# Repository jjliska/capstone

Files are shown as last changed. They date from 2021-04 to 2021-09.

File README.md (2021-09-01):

# AME 486 - Capstone - Reflection  

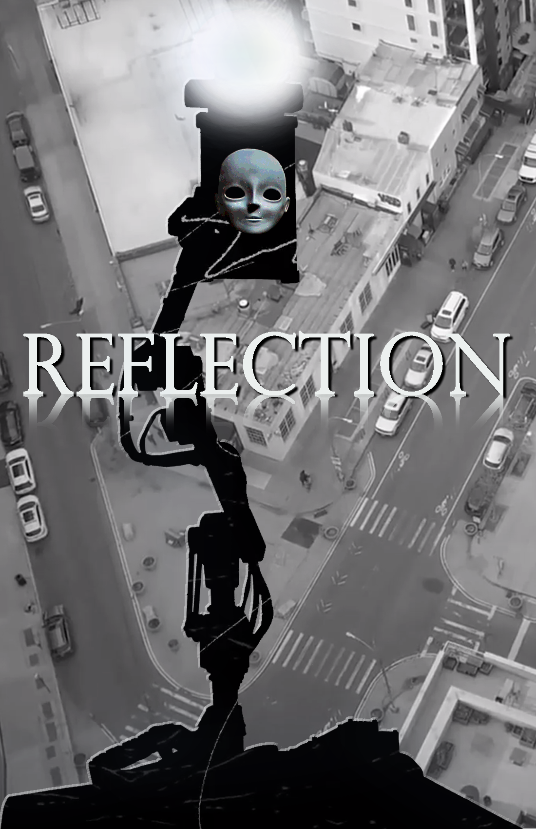
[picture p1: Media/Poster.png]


#### Table of Contents  
&ensp;[Group Members](#Group-Members)  
&ensp;[Project Description](#Project-Description)  
&ensp;[Capstone Video](#Capstone-Video)  
&ensp;[Improvements and Issues](#Improvements-and-Issues)  
&ensp;[Demo Videos](#Demo-Videos)  
&ensp;[Explanations](#Explanations)  
&ensp;[Links](#Links)  
&ensp;[References](#References)  

## Project Description  
&ensp;"Reflection" is an immersive, interactive art instillation that attempts to give people a form of interaction during isolation. The installation consists of two key components, the user and the robot cordially named Dum-E. Users interact with the piece by walking around in the scene, and looking at the robot. The machine learning algorithms will attempt to follow the person in the scene and react to their location and emotion. When Dum-E identifies a new emotion it will react with its own emotion and play a song at a specific location given where the user is.

## Group Members  
&ensp;<sup>[Back to Top](#AME-486---Capstone---Reflection)</sup>  
&ensp;[Albert Bang](https://albertbang3000.wixsit.com/) - Unity/Animator  
&ensp;[Ivan Mendoza](https://ivanmendozaportfolio.com/) - Programming/Building  
&ensp;[Jack Carroll](https://soundcloud.com/sodonttalksmack) - Sound Designer  
&ensp;[Joshua Liska](https://www.linkedin.com/in/joshua-liska-34a4b77b/) - Programming/Design/Engineering/Documentation

## Capstone Video  
&ensp;<sup>[Back to Top](#AME-486---Capstone---Reflection)</sup>  
IMAGE ALT TEXT HERE (https://www.youtube.com/watch?v=mnH26vL3UBw)

## Improvements and Issues  
&ensp;<sup>[Back to Top](#AME-486---Capstone---Reflection)</sup>  
#### Quick Links for Issues
&ensp;[Emotion and Facial Tracking](#Emotion-and-Facial-Tracking)  
&ensp;[Serial Read Issue](#Serial-Read-Issue)  
&ensp;[Speed Under Load](#Speed-Under-Load)  
&ensp;[Thermal Deformation](#Thermal-Deformation)  
#### Emotion and Facial Tracking  
##### The Problem  
&ensp;The consistency of the facial tracking system we used was not the most precise due to several reasons. One such reason, we suspect, is the camera quality was reduced so that it would run faster, as well as the dataset we used was most likely not precise enough for the system.  
&ensp; Another issue we faced was the lag caused by the emotion rendering system. We ended up setting this to run four to six times a minute for multiple reasons. One being the speed of the program was greatly increased when the emotions were only extracted several times a minute as well as the facial expressions of the unity program were allowed time to gently fade into each other. The emotion tracking was also not the most consistent, the dataset we used returned a roughly 66% accurate reading. It also has particular issues tracking emotion if there isn't enough light, hence the addition of a light on top of the arm.
##### Potential Solutions   
&ensp;A solution is to use a far more powerful computer to render the program in. This would allow for greater frame rates as well as being able to render emotions more accurately. A good small form factor computer for this would be an nvidia jetson, although it is an arm architecture processor, which would force us to either recompile the unreal engine source into an aarch64 architecture. We attempted to do this as well as exporting a unity project as an apk to run on android 11, however it didn't work as there were driver conflicts. 
&ensp;The facial expression detection dataset should be trimmed and retrained to allow for better facial expression tracking specifically in low light conditions and retrain it with our faces as a training set. We could also use some sort of recursive learning that retrains the model once a given number of facial frames are taken from the camera. This would require quite a substantial amount of processing power though to allow everything else to run efficiently.
#### Serial Read Issue
##### The Problem  
&ensp;There seems to be an issue with the Serial.Read on the microcontroller, for some reason even when reading bytes and converting to a data structure it will occasionally throw an error. This will end up crashing the program, and was initially the reason we needed so many try-catch and an eeprom safety net for if the program were to crash we could smoothly go back to the starting position and restart the program.
##### Potential Solutions  
&ensp;From many of the statements online this seems to be an issue with the arduino String data structure and it occasionally corrupts the memory. That being said we have a one way serial communication and the python program, running on a seperate computer, is crashing first. As of yet we do not have a concrete solution, simply possible conjecture that may help lead to a solution.
#### Speed Under Load  
##### The Problem  
&ensp;The speed is greatly affected under the complete load of the arm, roughly 1.3kgs. This causes us to either offset the amount of smoothness in the arm to consistently track the face, or to reduce the speed. We chose to reduce both slightly so they remain hand in hand. We attempted to limit this effect by creating a smoothing algorithm that attempted to take this into account.  
&ensp;[Smoothing Algorithm](#Smoothing-Algorithm)  
##### Potential Solutions   
&ensp;The solution is to, again, increase the torque of the motors so that they are constantly running efficiently and are not being damped by the load on the system. This would allow them to greatly increase their speed and accuracy while still maintaining a level of smoothness. To accomplish the amount of speed and accuracy for a real world application this item would need roughly a1 = 80kgs/cm, a2 = 60kgs/cm, a3 = 40kgs/cm, and a4 = 40kgs/cm. However these would most likely not be servo motors as stepper motors would allow us much more versatility than the servos, as well as a much sturdier mounting system through their metal chassis.
#### Thermal Deformation  
##### The Problem  
&ensp;Since everything was printed in PLA there wasn't much resistance to the motor reaching peak torque and amperage pull began giving off a lot of heat. This then caused the PLA to deform under tension, as it is being pulled between the gear and the tensioning bracket. This caused warping in the form of the motor mount which eventually led to a loss of torque as the motor would pull forward and loosen tension on the belt, forcing the arm to skip steps.
##### Potential Solutions  
&ensp;The solution would be to either print the part in a different material, such as ABS which has higher thermal resistance or, as a more long term solution, replacing a2 (the middle arm motor) with a higher torque motor so it is more efficient under load.

## Demo Videos
&ensp;<sup>[Back to Top](#AME-486---Capstone---Reflection)</sup>  
### Unity Demo
IMAGE ALT TEXT HERE (https://www.youtube.com/watch?v=sWtO3qcnU5k)
### Tracking Demo
IMAGE ALT TEXT HERE (https://www.youtube.com/watch?v=6vG7myi-orQ)
### Smoothing Demo
IMAGE ALT TEXT HERE (https://www.youtube.com/watch?v=c3GQ3jPTU7w)
### Alpha Demo
IMAGE ALT TEXT HERE (https://www.youtube.com/watch?v=l52GL87oeng)

## Explanations
&ensp;<sup>[Back to Top](#AME-486---Capstone---Reflection)</sup>

#### Quick Links for Explanations
&ensp;[End Effector](#End-Effector)  
&ensp;[Machine Learning Data](#Machine-Learning-Data)  
&ensp;[ML Facial Data to Movement](#ML-Facial-Data-to-Movement)  
&ensp;[Smoothing Algorithm](#Smoothing-Algorithm)  
&ensp;[Hardware](#Hardware)  
&ensp;[Other Explanations](#Other)  

### End Effector
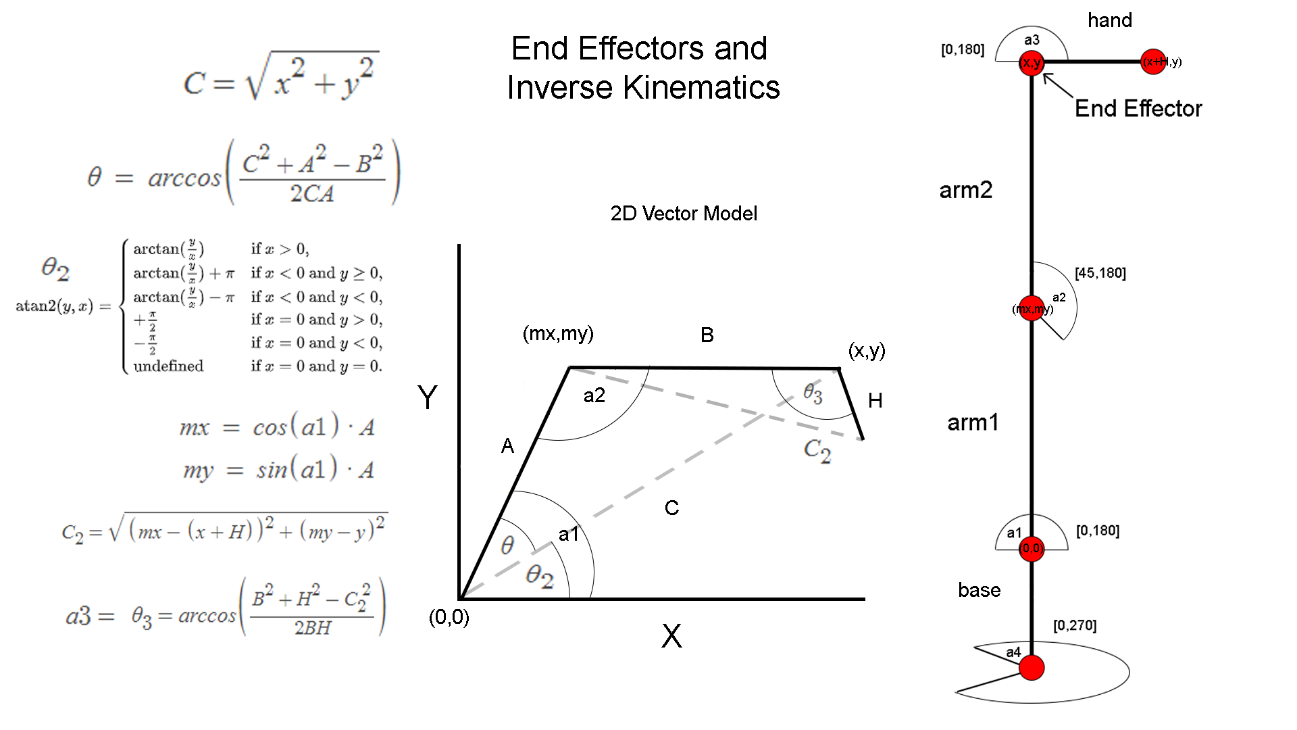
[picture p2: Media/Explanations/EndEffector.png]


&ensp;Inverse kinematics works via the premise that you know the base is 0,0 and the end effector is at some given point (x,y). Every shape can be then broken into triangles which have a given total angle. You can then determine this angle using the law of tangents and law of cosines. These allow you to determine the angle given arm lengths and positional data. For example, our arm has four degrees of freedom, three in the X and Y plane and one in the Z plane. We use two of the degrees of freedom to extend and retract the arm and a third to stabilize the "hand" and LCD attached to it. The fourth degree of freedom is used for Z rotation which is a simple trigonometry sin and cos function to calculate where the point is in a 3d space.

<details><summary>Python Script</summary>
<p>
  
```python
def lawOfCosines(a,b,c):
  return np.arccos((a**2+b**2-c**2) / (2.0*a*b))

def distance(x1,y1,x2,y2):
  return np.sqrt((x1-x2)**2+((y1-y2)**2))

def distanceMidArm(angle):
  opp = np.cos(angle) * arm1
  adj = np.sin(angle) * arm1
  return opp, adj

...

def angles(x,y):
  dist = distance(x,y,0,0)
  D1 = np.arctan2(y,x)
  D2 = lawOfCosines(dist,arm1,arm2)
  A1 = D1 + D2
  A2 = lawOfCosines(arm1,arm2,dist)
  return A1, A2
  
def rotateX(ox,x,angle):
  return ox+np.cos(angle)*(x-ox)

def rotateZ(ox,x,angle):
  return np.sin(angle)*(x-ox)
  
...
  
a1, a2 = angles(x,y)
mx, my = distanceMidArm(a1)
dist = distance(mx,my,x+hand,y)
#a3 is between arm2 and hand
if my <= y:
  a3 = lawOfCosines(arm2,hand,dist)
else:
  a3 = np.radians(360)-lawOfCosines(arm2,hand,dist)

#a4 is z rotation
a4 = np.radians(zRotation)
```

&ensp;[From capstoneV12_FINAlRELEASE.py](https://github.com/jjliska/capstone/blob/main/Code/Python/capstoneV12_FINALRELEASE.py)

</p>
</details>

### Machine Learning Data  
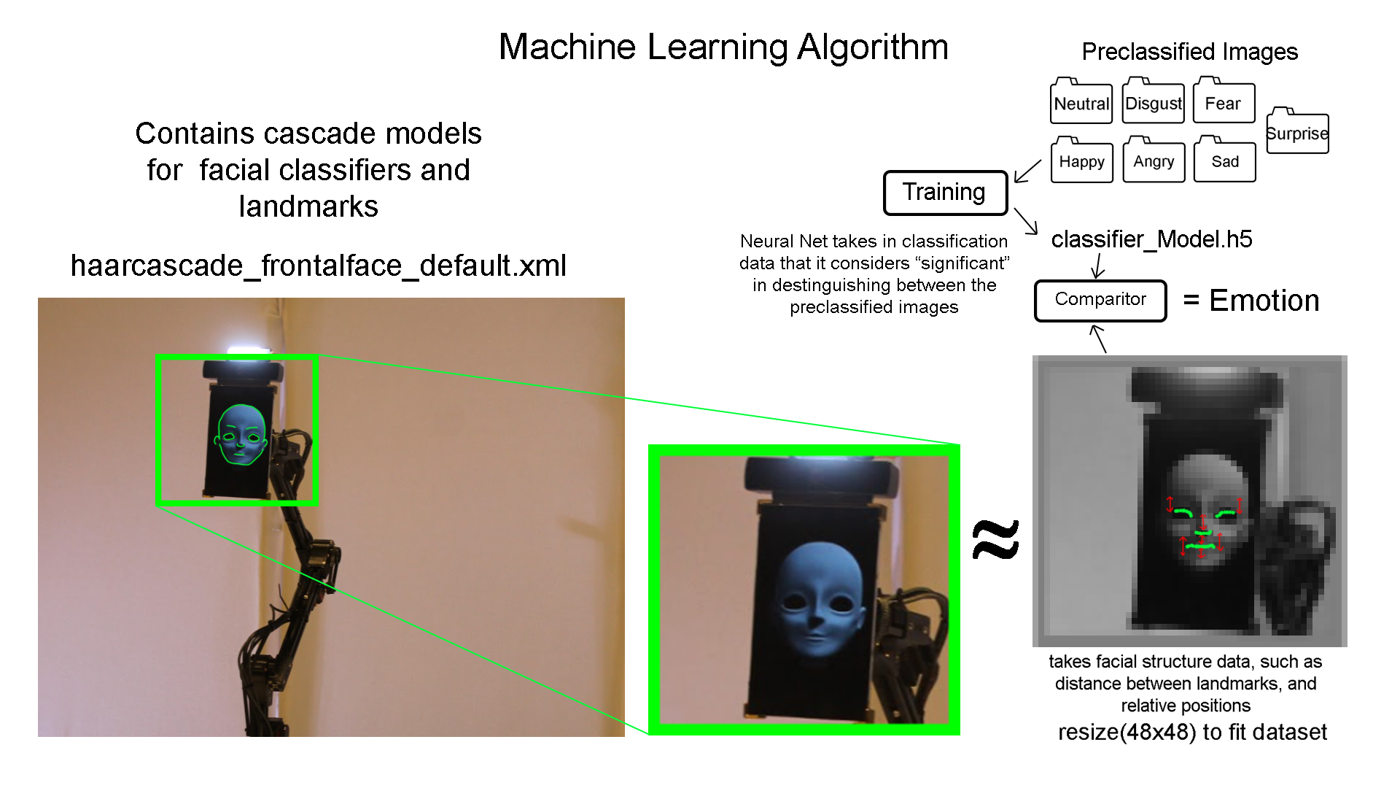
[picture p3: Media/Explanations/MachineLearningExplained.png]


&ensp;We use a pre classified dataset available in the openCV library, this is a visual library for machine learning. The pre classified haarcascade_frontalface_default.xml has pre classifications for significant landmarks of the face, for instance the edge of the face is a fairly distinct shape that can be recognized as separate from most objects in everyday life. This allows us to find exactly in frame where the face is. It returns a face(x,y,w,h) object that gives us facial bounding data. We then use that box created by the openCV haarcascade to crop out what we consider the "face" and convert it into a 48x48 pixel image. This is then passed to a classifying model that finds facial data points and compares it to another pre classified model that contains definitions for "emotion" which is a fairly hard for computer vision to assume. This is due to many people having different facial structures and what they consider the emotion on their face. Although this is fairly hard the trained model we used had a 66% accuracy. Althought it often tended to find that I was angry, as my neutral face looked angry to it.

<details><summary>Python Script</summary>
<p>

```python
cascPath = "haarcascade_frontalface_default.xml"
faceCascade = cv2.CascadeClassifier(cascPath)
modelPath = "model_35_91_61.h5"
emotion =  ['Anger', 'Disgust', 'Fear', 'Happy', 'Sad', 'Surprise', 'Neutral']
model = keras.models.load_model(modelPath)

...

    gray = cv2.cvtColor(frame, cv2.COLOR_BGR2GRAY)

    # Sets the face to gray, scales it, and then sets min neighbor and min size
    # These all help in removing false positives that the program sees and to reduce error.
    faces = faceCascade.detectMultiScale(
      gray,
      scaleFactor=1.2,
      minNeighbors=10,
      minSize=(30, 30)
    )

...

    # Draw a rectangle around the faces
    for (x, y, w, h) in faces:
      # Every second get the emotion written on the face via a 48*48
      # "facial structure" which pulls bounding data and refers to a trained model
      if getMood:
        # Gets the face, sets it to a 48*48 size frame and then parses it into
        # the model to attempt to find what expression is being stolen
        face_component = gray[y:y+h, x:x+w]
        fc = cv2.resize(face_component, (48, 48))
        inp = np.reshape(fc,(1,48,48,1)).astype(np.float32)
        inp = inp/255.
        prediction = model.predict(inp)
        em = emotion[np.argmax(prediction)]
        facialEmotion = em
        getMood = False

      # Draw the standard rectangle and store facial data in the facePos array
      cv2.rectangle(frame, (x, y), (x+w, y+h), (0, 255, 0), 2)
      if not (x,y,w,h) == (0,0,0,0):
        facePos = (x,y,w,h)
      break
```

&ensp;[From capstoneV12_FINAlRELEASE.py](https://github.com/jjliska/capstone/blob/main/Code/Python/capstoneV12_FINALRELEASE.py)

</p>
</details>

### ML Facial Data to Movement
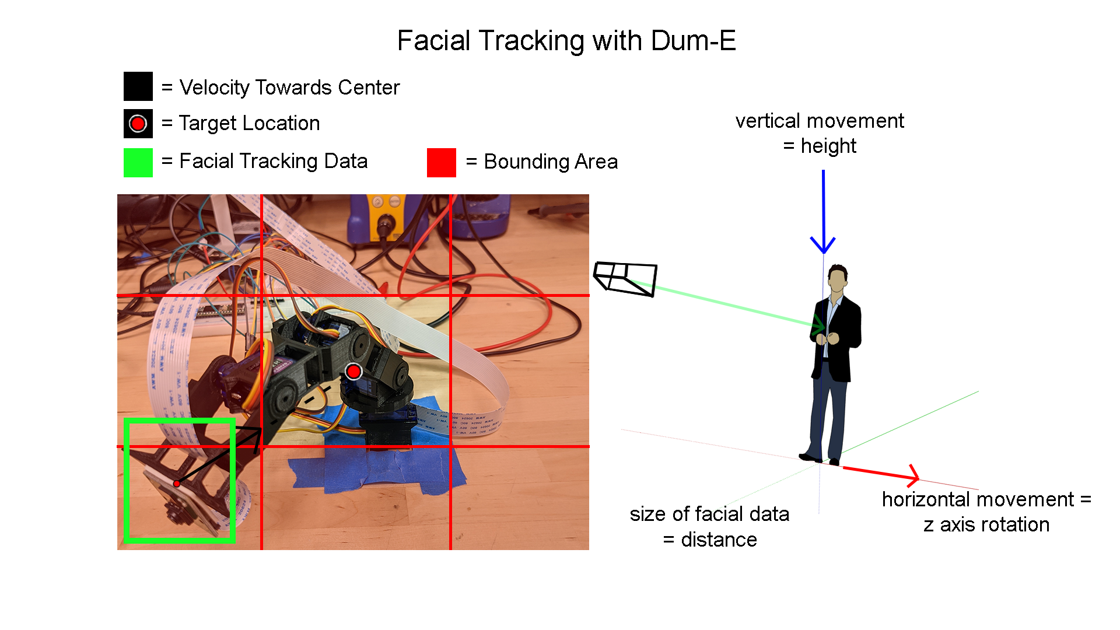
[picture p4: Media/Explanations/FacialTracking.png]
  

&ensp;The machine learning algorithm detects the face and then sends that data to an algorithm that determines where in the camera's lense the person is. It then determines where it should move to and how quickly given previous movement and the distance from the center of the camera. This then allows the camera to attempt to position itself over the center of the users face. This allows the program to better recognize the user's emotional state as there is no distortion in the image or partial faces.  
&ensp;- Vertical movement in the camera translates to vertical of the arm.  
&ensp;- Horizontal movement in the camera's plane translates to rotational movement of the base, a4.  
&ensp;- The bounding size of the facial data translates to depth of the arm.  

<details><summary>Python Script</summary>
<p>

```python
def facePosHandler():
  # x axis of camera is z axis of robot
  # y axis of camera is y axis of robot
  # size of facial bounding box is the x axis of robot

  if noFaceDetected < noFaceTime:
    z1C, y1C = getCenterBox()
    x1C = facePos[2]
    tempX,tempY,tempRotZ = 0,0,0
    # Z rotation
    if z1C >= boundsRight:
      tempRotZ = velocityHandler(2,-1)
    elif z1C <= boundsLeft:
      tempRotZ = velocityHandler(2,1)
    else:
      tempRotZ = velocityHandler(2,0)

    # Y movement
    if y1C >= boundsTop:
      tempY = velocityHandler(1,1)
    elif y1C <= boundsBottom:
      tempY = velocityHandler(1,-1)
    else:
      tempY = velocityHandler(1,0)

    # X movement
    if x1C >= boundsNear:
      tempX = velocityHandler(0,-1)
    elif x1C <= boundsFar:
      tempX = velocityHandler(0,1)
    else:
      tempX = velocityHandler(0,0)
  else:
    tempX = velocityHandler(0,0)
    tempY = velocityHandler(1,0)
    tempRotZ = velocityHandler(2,0)

  if not tempX == 0 or not tempY == 0 or not tempRotZ == 0:
    updateVariables(x+tempX,y+tempY,zRotation+tempRotZ)
```

&ensp;[From capstoneV12_FINAlRELEASE.py](https://github.com/jjliska/capstone/blob/main/Code/Python/capstoneV12_FINALRELEASE.py)

</p>
</details>

### Smoothing Algorithm
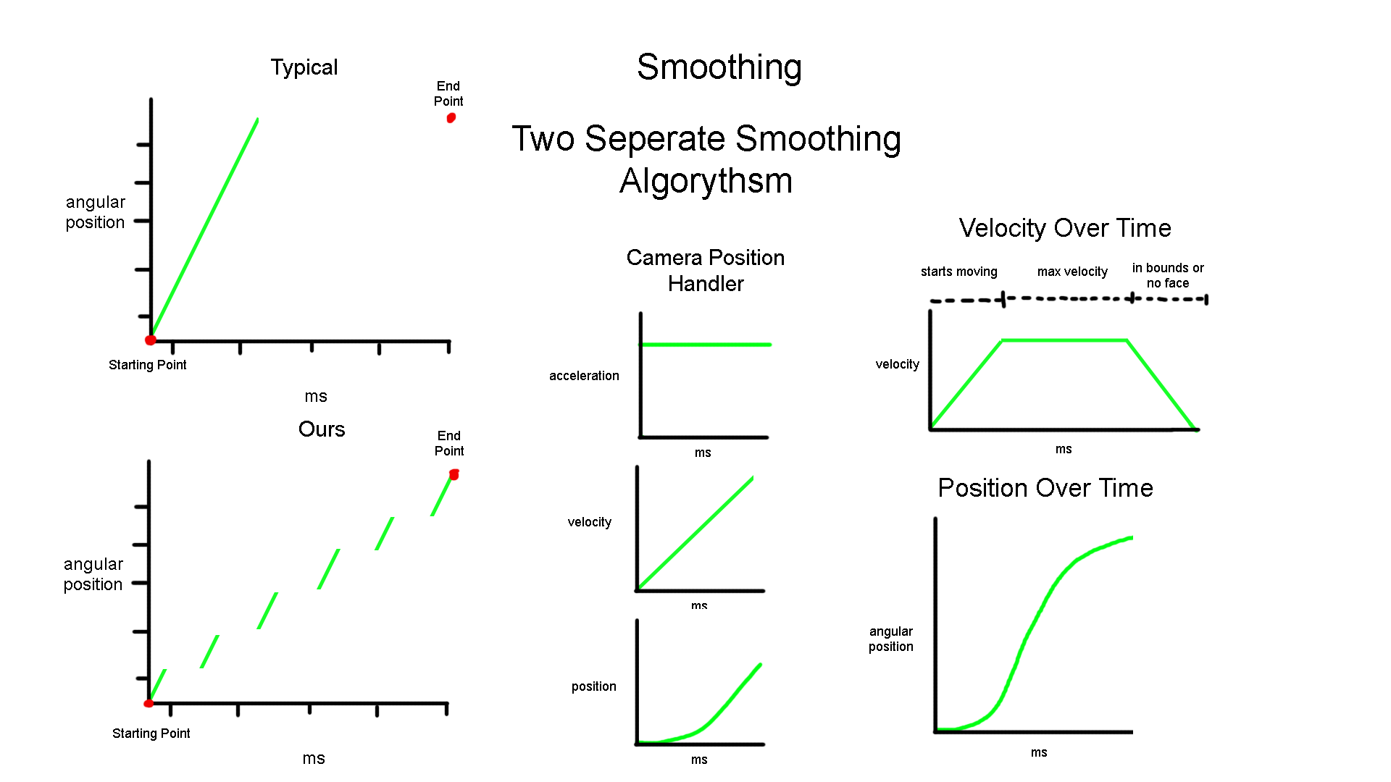
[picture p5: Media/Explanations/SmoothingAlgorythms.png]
  

&ensp;We use two seperate smoothing algorithms to try and smooth the movement of the arm. The first is run on the python script which uses an acceleration equation to gently accelerate to a top velocity and then once it reaches the bounding box, or facial positioning data is no longer available, the velocity gently lowers back to zero. This allows the program to create a gentle start and stop for the end effector in which the first several steps will be slow and gently bring the arm up to full speed and then gently lower it back to speed to attempt to lessen damping and "bouncing" on the system. This allows us to achieve much faster speeds without sacrificing the precision of the facial tracking algorithm. Although this is a trade off, if it is too smooth it will not be fast enough, and if it is too fast it will not be smooth enough and begin overshooting and having to compensate.    

<details><summary>Python Script</summary>
<p>

```python
smoothingValue = 10
maxVelocity = 0.49
rotationAdjustment = 2.0
velocity = [0.0,0.0,0.0]

# Handles acceleration and velocity to create a smooth start and stop
def velocityHandler(velNum,direction):
  global velocity
  if velNum == 2:
    accelVal = maxVelocity/smoothingValue
    maxVelocityAdjusted = rotationAdjustment*maxVelocity
  else:
    accelVal = maxVelocity/smoothingValue
    maxVelocityAdjusted = maxVelocity
  # No face detected or the face is in the bounds deaccelerate
  if noFaceDetected > noFaceTime or direction == 0:
    if velocity[velNum] >= -1*accelVal and velocity[velNum] <= accelVal:
      velocity[velNum] = 0
    elif velocity[velNum] > 0:
      velocity[velNum] -= accelVal
    elif velocity[velNum] < 0:
      velocity[velNum] += accelVal
  # Increases acceleration to create and easing effect on the servos so they do not immediately start jumping to large degree of angle changes
  else:
    if direction == -1 and velocity[velNum] > -1*maxVelocityAdjusted:
      velocity[velNum] -= accelVal
    elif direction == 1 and velocity[velNum] < maxVelocityAdjusted:
      velocity[velNum] += accelVal
  return velocity[velNum]
```

&ensp;[From capstoneV12_FINAlRELEASE.py](https://github.com/jjliska/capstone/blob/main/Code/Python/capstoneV12_FINALRELEASE.py)

</p>
</details>

&ensp;The second smoothing algorithm is important for several reasons. One is that the python program is not running over every microsecond to gently smooth the servos angular position to the desired position. Thus we need to feed data for a microcontroller and smooth on that microcontroller. Servos do not have a set speed so instead we can use writeMicroseconds() to get a much finer angular translation. We can then take inputs from the python every ~10 milliseconds and smooth it over that given amount of time, recalculation where the angle needs to be at to gently smooth the arm between a given input(a[num]) and the current angle(cura[num]). Typically a servo would instead move to the desired position it was fed(a[num]) as fast as it could while ours attempts to smooth it to closer fit the acceleration model in the python.

<details><summary>C/C++ Script</summary>
<p>

```c
const int delayTime = 100;

//Average time (in ms) between serial.write() on python script
const int timeForMessages = 10000;

//Rate of which the machine is smoothed so i runs every "millisecond" it could run faster
//to create even smoother lines but since its run on parsecs and we only have a degree of
//accuracy of about 1.2 +- some deflection it should be fine 
const float smoothingRate = float(delayTime)/float(timeForMessages);

...

float moveToAngle(float input, float currentAngle, Servo servoName){
  float retFloat;
  float difference = abs(input-currentAngle);
  if(currentAngle > input){
    if((currentAngle - input) > (difference*smoothingRate)){
      retFloat = currentAngle-(difference*smoothingRate);
      writeToServo(servoName,retFloat);
      return retFloat;
    }
    else{
      writeToServo(servoName,input);
      return input;
    }
  }
  else if(currentAngle < input){
    if((currentAngle - input) < (-1*(difference*smoothingRate))){
      retFloat = currentAngle+(difference*smoothingRate);
      writeToServo(servoName,retFloat);
      return retFloat;
    }
    else{
      writeToServo(servoName,input);
      return input;
    }
  }
}
```

&ensp;[From ServoController.ino](https://github.com/jjliska/capstone/blob/main/Code/ServoController/ServoController.ino)

</p>
</details>

### Hardware
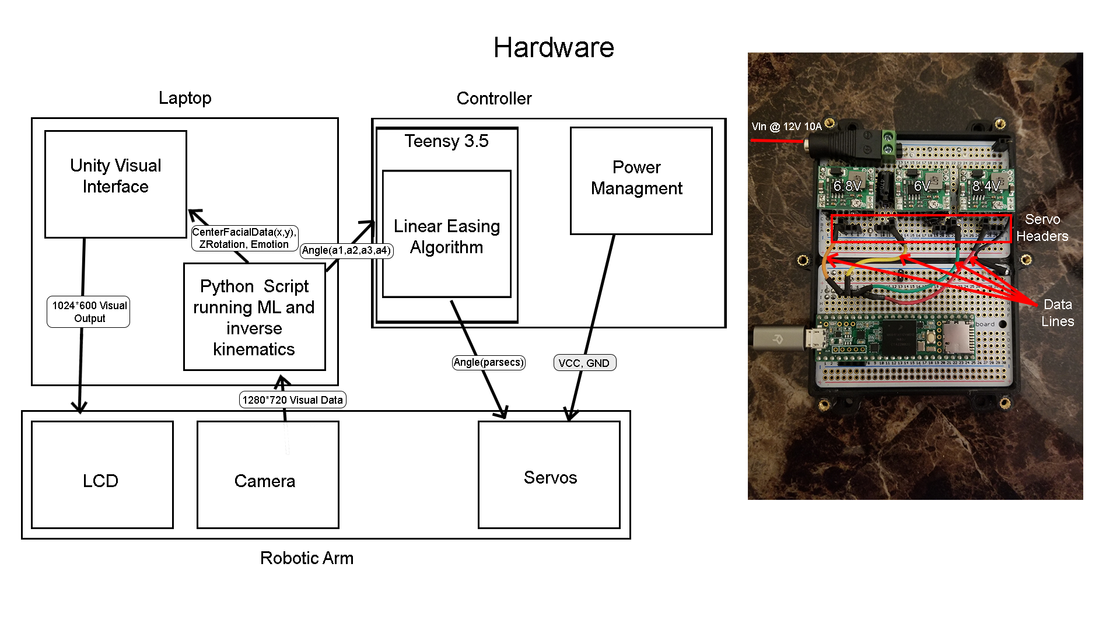
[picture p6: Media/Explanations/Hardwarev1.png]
  

&ensp;We use a python script running on a laptop that draws information from a generic USB webcamera. The USB webcam passes visual information into a machine learning script that then creates a generic rectangle over the given persons face given the size and position of the face. This information is then stored and used by the script to effect the end effector. We do this to stabilize the LCD so that the interaction on the display is more stable for the user. The python script works by creating a vector model from given initial information along with the facial bounding box. This information includes length, mass, torque, and angular hard limits of the system. The system then determines what the maximum amount of force it can put on its joints before the motors will begin to slip. This information is then used in an inverse kinematic model ([stated in the End Effector](#End-Effector) portion of the explanation) of the robotic arm in which the end effector is moved inside of a 3D model to determine what the angles between the arms are. The information is then passed from this python script to a Teensy 3.5 in order to utilize pwm and additional vector smoothing.

### Other
#### Angular Memory in the Event of a Crash
&ensp;We attempt to stop the robot from seriously damaging itself in the event that the script throws an error. This saves the angular information every several seconds so that, if the program is restarted it will then attempt to rehome to a set location from the stored angular data.

<details><summary>C/C++ Script</summary>
<p>

```c
if(millis()-eepromTimer >= eepromDelay){
  writeStringToEEPROM(0, eepString);
}

String readStringFromEEPROM(int addrOffset){
  int newStrLen = EEPROM.read(addrOffset);
  char data[newStrLen + 1];
  for (int i = 0; i < newStrLen; i++){
    data[i] = EEPROM.read(addrOffset + 1 + i);
  }
  data[newStrLen] = '\0';
  return String(data);
}

void writeStringToEEPROM(int addrOffset, const String &strToWrite){
  byte len = strToWrite.length();
  EEPROM.write(addrOffset, len);
  for (int i = 0; i < len; i++){
    EEPROM.write(addrOffset + 1 + i, strToWrite[i]);
  }
}

```

&ensp;[From ServoController.ino](https://github.com/jjliska/capstone/blob/main/Code/ServoController/ServoController.ino)

</p>
</details>

#### Changing Facial Expression and Direction
&ensp;We attempt to change the facial expression of the face model using facial data from the python script. This allows us to recreate the actors facial expression and try to interact with them visually and mimic their expressions. We also change the target location of a armature deform to direct the face in a specific direction to look at the user while the arm moves to them. This gives the user the impression the arm is looking directly at them while it moves to center their face.

<details><summary>C# Script</summary>
<p>

```cs
    TargetPosition = new Vector3(-1*x/25.0f, y/25.0f, zConst);
    transform.position = TargetPosition;
    
...

  private void emotionHandler(){
    if(previousEmotion == ""){
      if(blendEmotion < blendFaceStop){
        blendEmotion += blendSpeedEmotion;
        emotionCase(emotion);
      }
      else{
        previousEmotion = emotion;
      }
    }
    else{
      if(previousEmotion != emotion){
        if(blendEmotion > 0f){
          blendEmotion -= blendSpeedEmotion;
          emotionCase(previousEmotion);
        }
        else{
          previousEmotion = emotion;
        }
      }
      else{
        if(blendEmotion < blendFaceStop){
          blendEmotion += blendSpeedEmotion;
          emotionCase(emotion);
        }
      }
    }
  }
  
...

  private void emotionCase(string input){
    //Determining which object is active/visible in the scene
    if(input == "Fear"){
      humanFaceParent.active = false;
      gasMaskParent.active = true;
    }
    else{
      humanFaceParent.active = true;
      gasMaskParent.active = false;
    }

    //Emotion Case to identify what needs to happen visually to interact with the user
    switch(input){
      case "Anger":
        skinnedMeshRenderer.SetBlendShapeWeight(0, blendEmotion);
        break;
      case "Disgust":
        skinnedMeshRenderer.SetBlendShapeWeight(3, blendEmotion);
        skinnedMeshRenderer.SetBlendShapeWeight(3, blendEmotion);
        break;
      case "Fear":
        gasMaskParent.active = true;
        break;
      case "Happy":
        skinnedMeshRenderer.SetBlendShapeWeight(2, blendEmotion);
        break;
      case "Sad":
        skinnedMeshRenderer.SetBlendShapeWeight(3, blendEmotion);
        break;
      case "Surprise":
        skinnedMeshRenderer.SetBlendShapeWeight(1, blendEmotion);
        break;
      case "Neutral":
        //Do nothing its a neutral expression
        break;
      default:
        humanFaceParent.active = true;
        break;
    }
  }
```

&ensp;[From UdpSockets.cs](https://github.com/jjliska/capstone/blob/main/Code/UnityCode/UdpSocket.cs)

</p>
</details>

#### Changing Music Based on Emotion and Location
&ensp;We take emotion and facial data from the python script and pass it to a rotation object as well as an audio object that allows us to change the music depending on the mood shown as well as changing location to be directly behind where the arm considers itself to create a more interactive environment.

<details><summary>C# Script</summary>
<p>
  
```cs
    audioRotation.transform.Rotate(0,rotation,0);
    
...

  private void musicHandler(){
    int compEmot = musicComparison(emotion);
    int compPreEmot = musicComparison(previousEmotion);
    if(compPreEmot == 0){
      if(volume < 1.0f){
        volume += volumeSpeed;
        musicCase(compEmot);
      }
    }
    else{
      if(compPreEmot != compEmot){
        if(volume > 0f){
          volume -= volumeSpeed;
          musicCase(compPreEmot);
        }
      }
      else{
        if(volume < 1.0f){
          volume += volumeSpeed;
          musicCase(compEmot);
        }
      }
    }
  }

  // Change this to add more audio tracks
  private void musicCase(int input){
    if(input != 0){
      if(input == 1){
        musicPlayer1.volume = volume;
      }
      else if(input == 2){
        musicPlayer2.volume = volume;
      }
      else if(input == 3){
        musicPlayer3.volume = volume;
      }
    }
  }

  // This is made easier to access to allow for more string comparisons as there may be a change to the audio track later
  private int musicComparison(string input){
    if(input == "Happy" || input == "Surprise"){
      return 1;
    }
    else if(input == "Anger" || input == "Disgust" || input == "Fear"){
      return 2;
    }
    else if(input == "Neutral" || input == "Sad"){
      return 3;
    }
    else{
      return 0;
    }
  }
```

&ensp;[From UdpSockets.cs](https://github.com/jjliska/capstone/blob/main/Code/UnityCode/UdpSocket.cs)

</p>
</details>

## Links
&ensp;<sup>[Back to Top](#AME-486---Capstone---Reflection)</sup>  
&ensp;- A collab with some of the basic inverse kinematic models we used is available here: [Google Colab](https://colab.research.google.com/drive/112x_Fhu4YKPZFFK7a1mo7FeFkNSDPJKg?usp=sharing)  
&ensp;- A link to all of the 3D printed parts we designed and printed: [3D Prints](https://github.com/jjliska/capstone/tree/main/3D-Prints)  
&ensp;- The Fusion 360 Model created: [Fusion 360](https://a360.co/3mX6sYx) &ensp;&ensp; *Note it is a large file so it will take a while to render on a browser.*  
&ensp;- A link to the FBX models, and shape keys attached to them, we created for this project: [Models](https://github.com/jjliska/capstone/tree/main/Media/FacialModels)  
&ensp;- A link to all the music created by Jack Carroll: [Soundcloud](https://soundcloud.com/sodonttalksmack/sets/reflection)  

## References
&ensp;<sup>[Back to Top](#AME-486---Capstone---Reflection)</sup>
#### &ensp;[Ender 3 Cable Chain](https://www.thingiverse.com/thing:2920060)
#### &ensp;[Emotion Model](https://drive.google.com/file/d/1192YC8mYKaCbCoACP8hTfr9PCMC2iN30/view?usp=sharing) from [jaydeepthik](https://github.com/jaydeepthik)
#### &ensp;[Face Detection](https://realpython.com/face-detection-in-python-using-a-webcam/)
#### &ensp;[Two-way communication between Python 3 and Unity (C#) - Y. T. Elashry](https://github.com/Siliconifier/Python-Unity-Socket-Communication.git)
#### &ensp;[Writing to EEPROM](https://roboticsbackend.com/arduino-write-string-in-eeprom/)

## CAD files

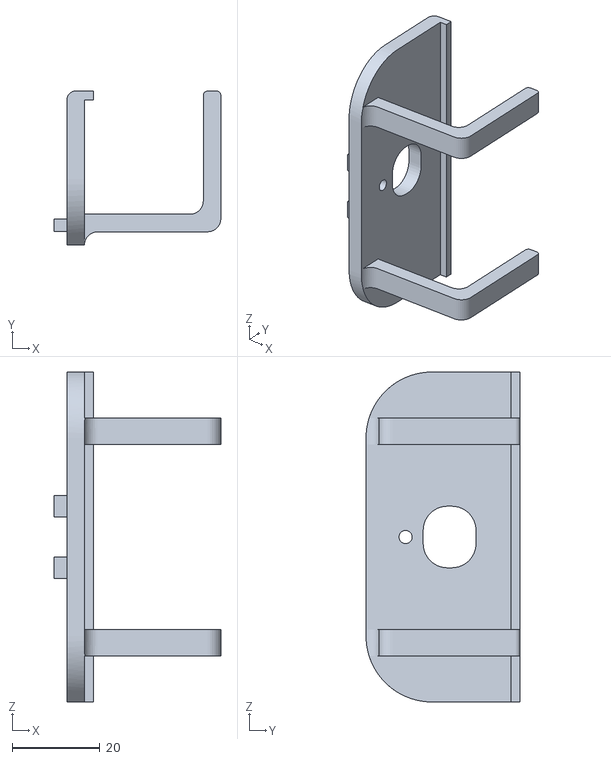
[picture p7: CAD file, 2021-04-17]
3D-Prints/LCD/FullSizeWebcam.stl
37.9 x 35.0 x 75.0

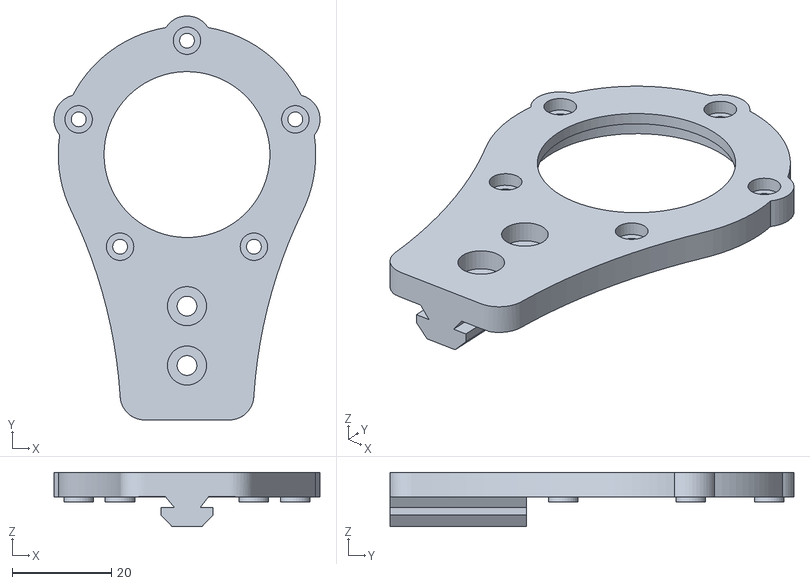
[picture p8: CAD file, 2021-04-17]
3D-Prints/ArmAxel/BearingFace2.stl
53.7 x 81.6 x 11.0

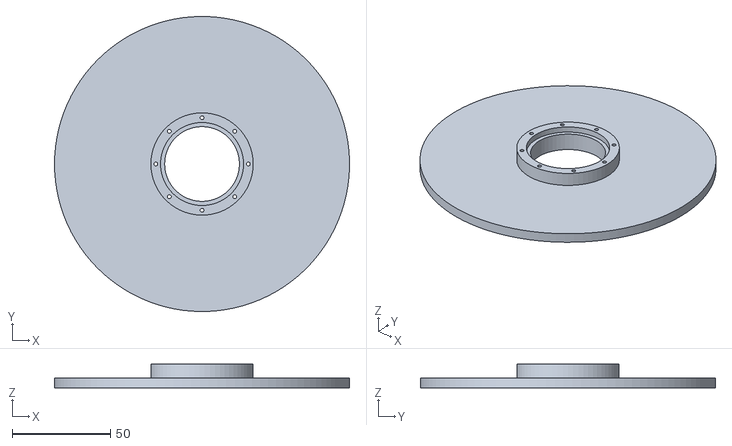
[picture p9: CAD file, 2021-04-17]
3D-Prints/BaseAxel/BaseSleeve_Bottom.stl
150.0 x 150.0 x 12.0

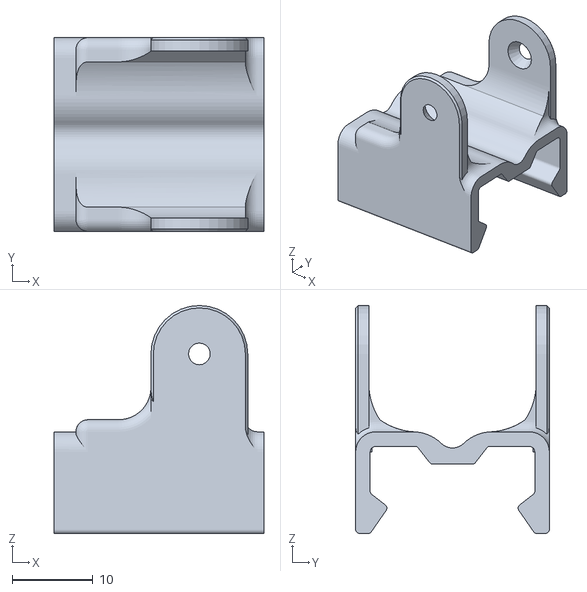
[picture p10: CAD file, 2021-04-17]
3D-Prints/Chain Adapters/20mmTSlotChainAdapter_Female.stl
26.0 x 24.0 x 28.2

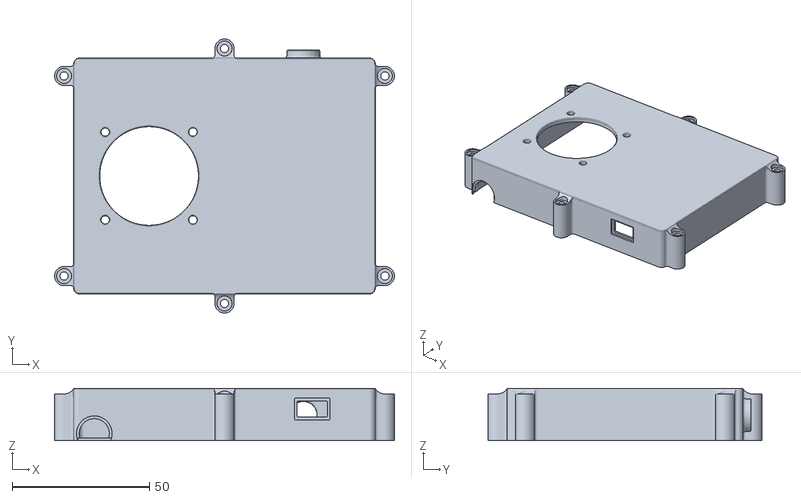
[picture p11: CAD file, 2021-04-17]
3D-Prints/DualBreakoutBoardCase/DualBreakoutBoardCaseTop.stl
124.0 x 100.0 x 19.0

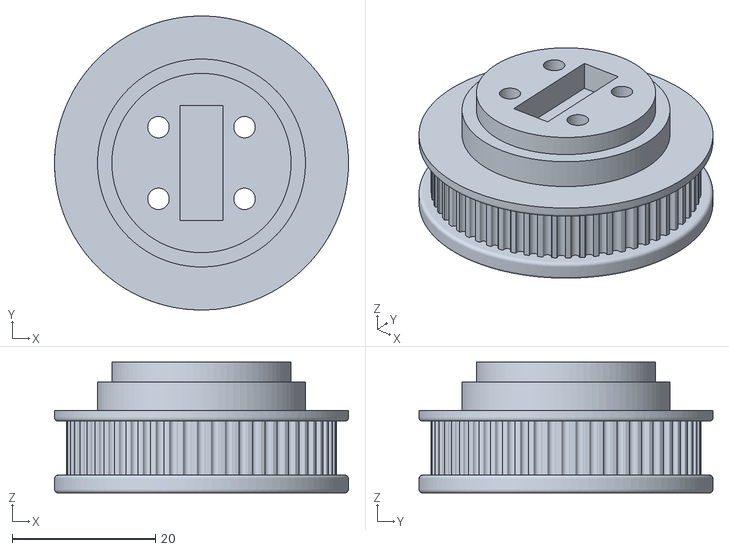
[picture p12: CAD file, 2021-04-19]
3D-Prints/Gears/60ToothMidArm.stl
41.0 x 41.0 x 18.2

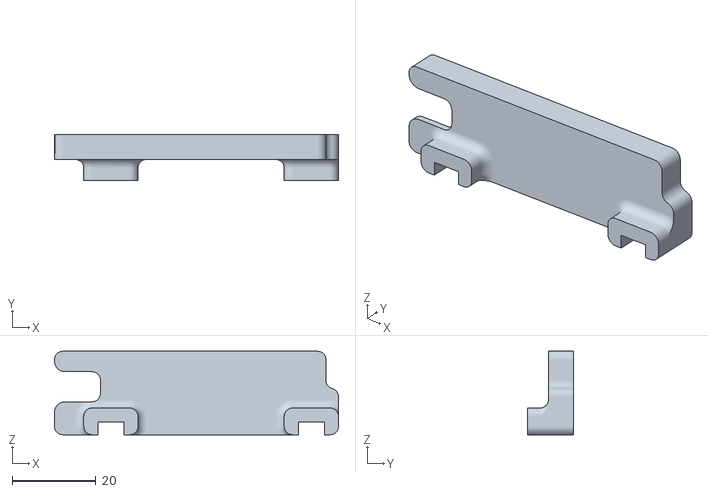
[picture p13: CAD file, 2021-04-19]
3D-Prints/LEDHolder/BackPlate.stl
68.0 x 11.0 x 20.0

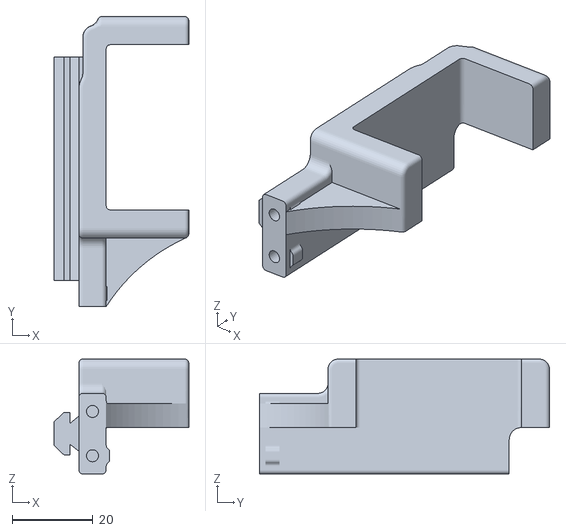
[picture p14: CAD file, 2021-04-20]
3D-Prints/Motor Mounts/25-35kgMountBeefy.stl
33.4 x 72.0 x 28.5

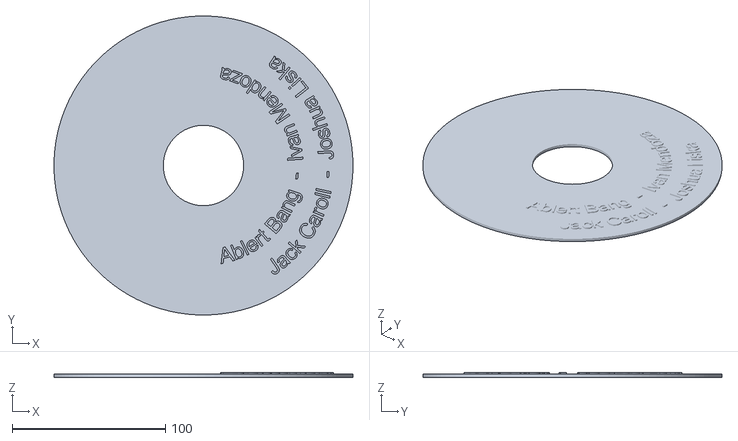
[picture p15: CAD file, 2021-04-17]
3D-Prints/NamePlates_Aesthetic/NamePlate.stl
195.0 x 195.0 x 3.00

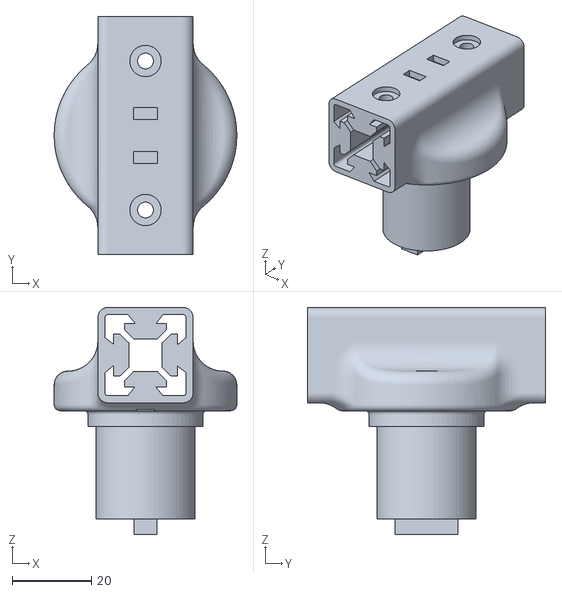
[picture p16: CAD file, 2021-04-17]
3D-Prints/ArmAxel/ArmAxel.stl
46.0 x 60.0 x 57.1

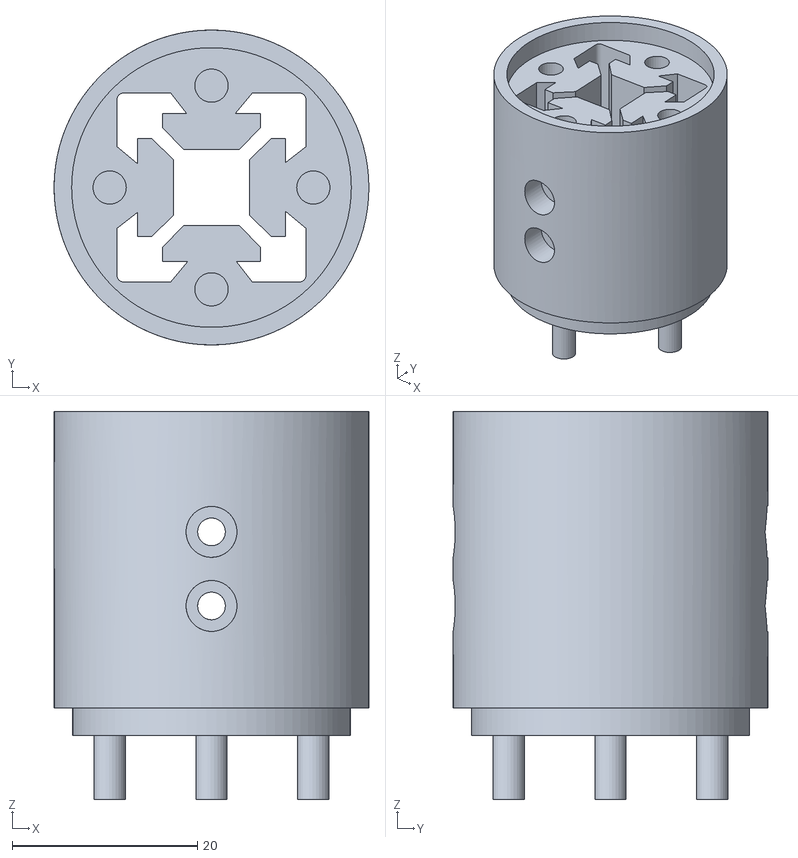
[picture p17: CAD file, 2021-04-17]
3D-Prints/BaseAxel/BaseAxel_Center_Top.stl
34.0 x 34.0 x 41.9

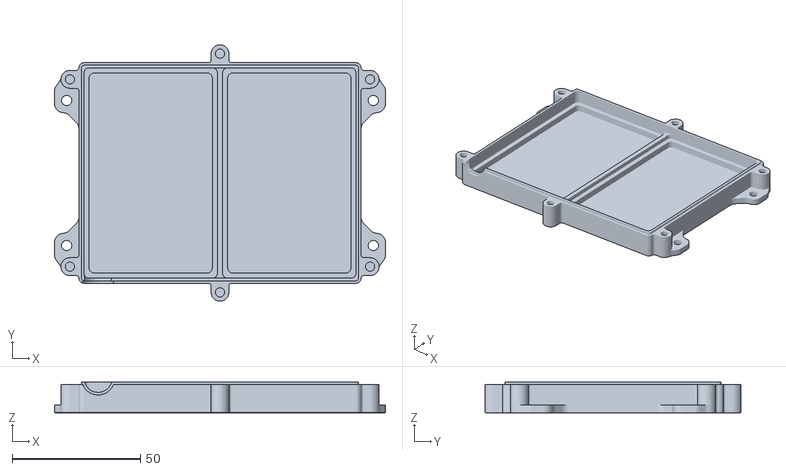
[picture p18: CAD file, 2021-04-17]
3D-Prints/DualBreakoutBoardCase/DualBreakoutBoardCaseBase.stl
129.0 x 99.9 x 12.0

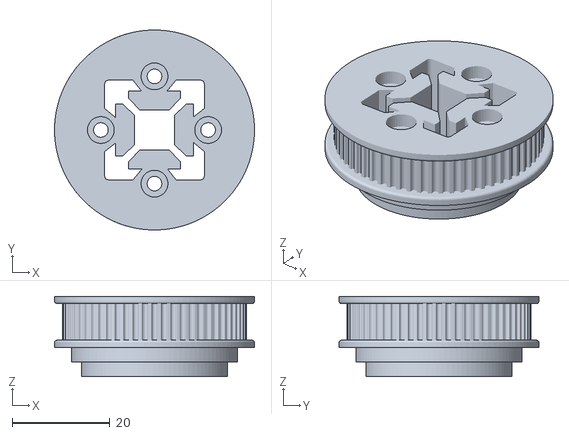
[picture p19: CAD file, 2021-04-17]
3D-Prints/Gears/60Tooth_BaseAxel.stl
41.0 x 41.0 x 16.5

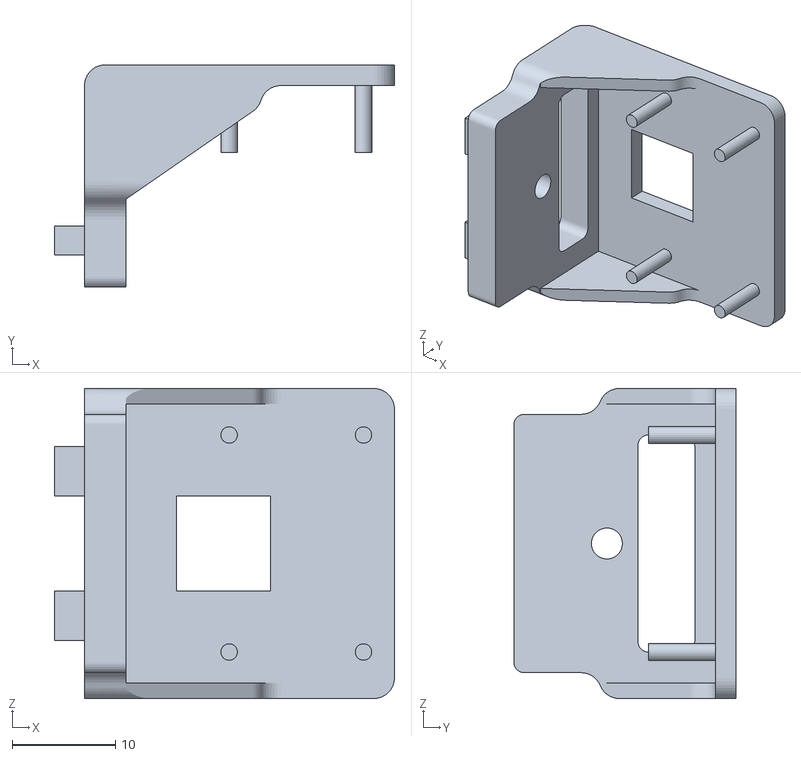
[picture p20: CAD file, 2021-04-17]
3D-Prints/LCD/PiWebcamMount.stl
32.9 x 21.5 x 30.0

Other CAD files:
3D-Prints/Chain Adapters/20mmTSlotChainAdapter_Female_90Degree.stl
3D-Prints/LEDHolder/Front Plate.stl
3D-Prints/Motor Mounts/Mount_60kg.stl
3D-Prints/ArmAxel/BearingFace1.stl
3D-Prints/ArmAxel/BearingCenter.stl
3D-Prints/BaseAxel/BaseAxel_Bottom.stl
3D-Prints/BaseAxel/BaseAxel_Center_Bottom.stl
3D-Prints/BaseAxel/BaseSleeve_Center.stl
3D-Prints/BaseAxel/BaseSleeve_Top_20mmTSlotMount.stl
3D-Prints/Chain Adapters/20mmTSlotChainAdapter_Male.stl
3D-Prints/Gears/30Tooth_25kg.stl
3D-Prints/Gears/30Tooth_60kg.stl
3D-Prints/Gears/45Tooth_ArmAxel.stl
3D-Prints/Gears/60Tooth_25kg.stl
3D-Prints/LCD/LCDBracket.stl
3D-Prints/LCD/LCDHolder.stl
3D-Prints/Motor Mounts/BaseMotorMount_25kg.stl
3D-Prints/Motor Mounts/MotorTensioner.stl
3D-Prints/Motor Mounts/MountExtended_25kg.stl
3D-Prints/Motor Mounts/Mount_25kg.stl
3D-Prints/NamePlates_Aesthetic/DumEEmblem.stl
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

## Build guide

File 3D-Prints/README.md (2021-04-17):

# Fusion 360 Models
### Models Created by Joshua Liska
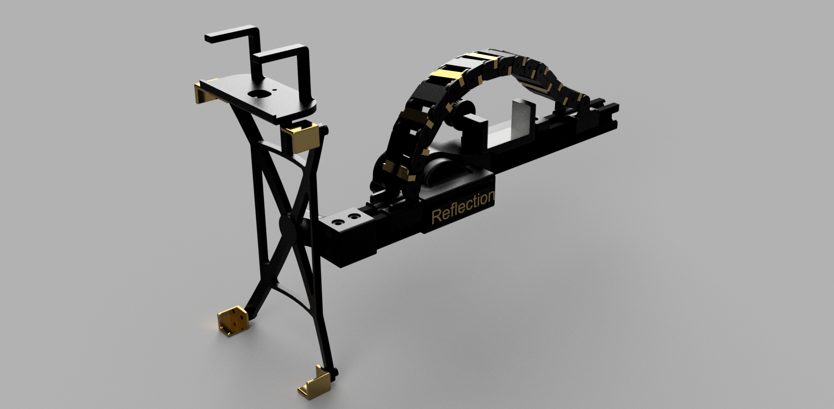
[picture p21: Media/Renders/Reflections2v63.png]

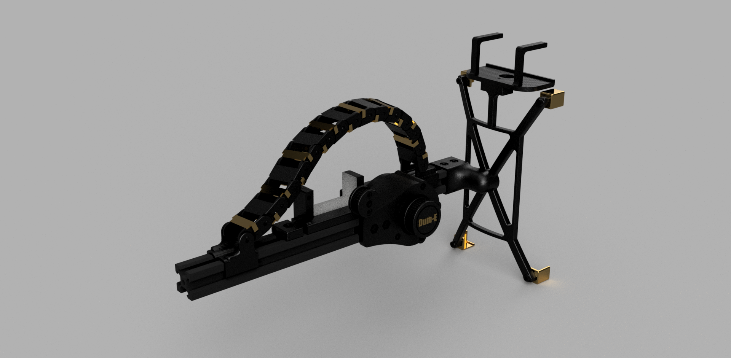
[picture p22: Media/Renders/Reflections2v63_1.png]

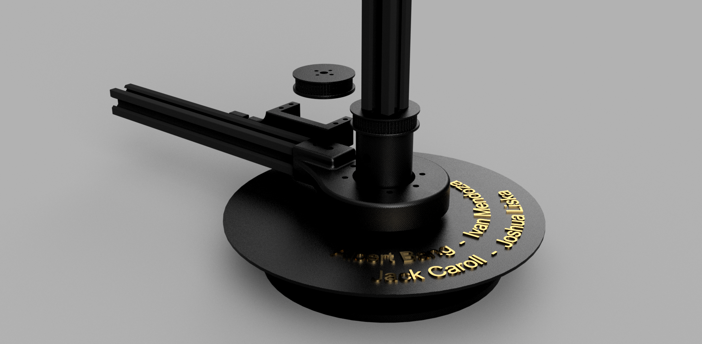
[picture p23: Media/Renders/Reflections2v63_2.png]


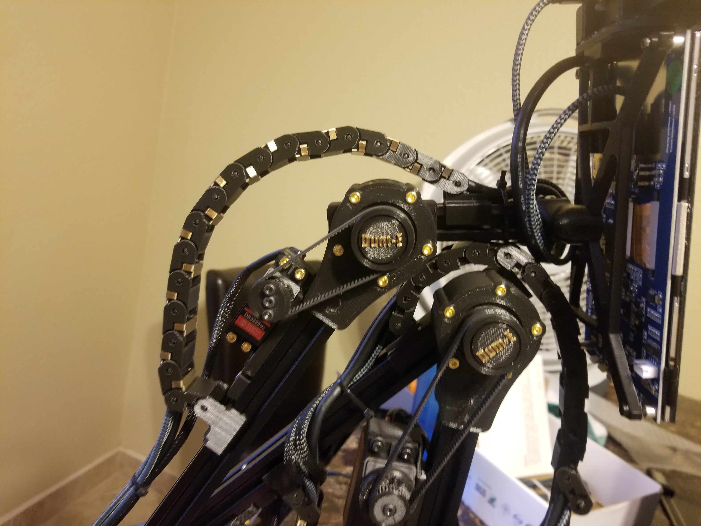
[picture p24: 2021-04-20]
Media/ArmBuild/5.jpg

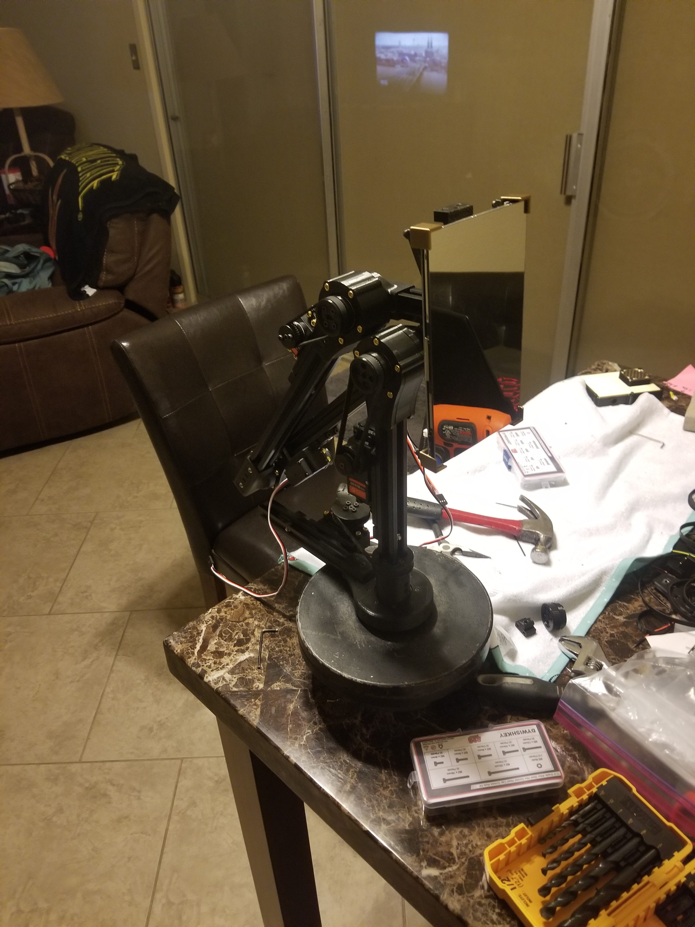
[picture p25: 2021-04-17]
Media/ArmBuild/3.jpg

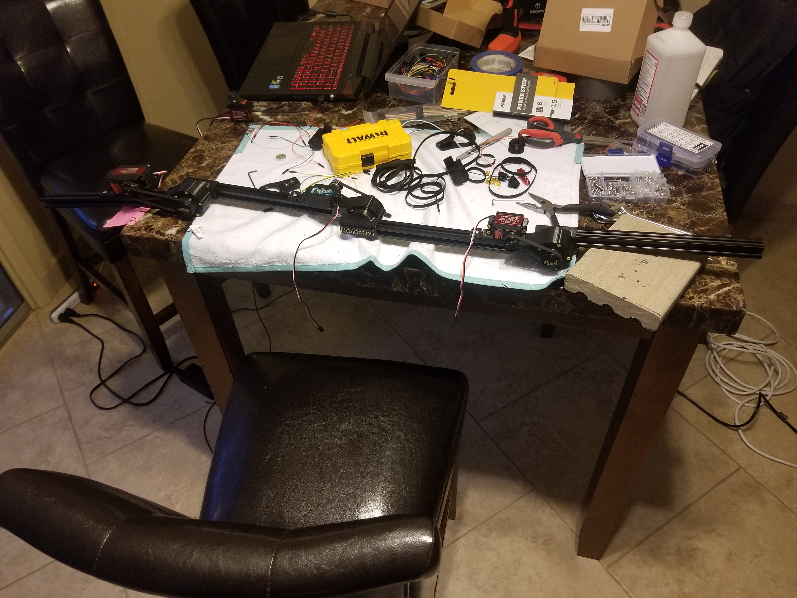
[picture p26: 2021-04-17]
Media/ArmBuild/2.jpg

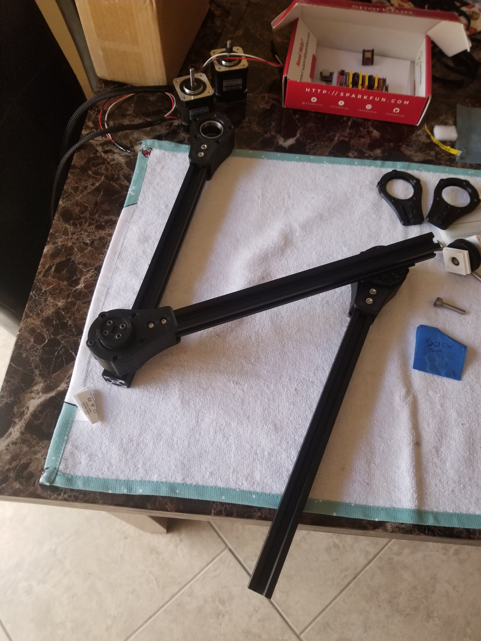
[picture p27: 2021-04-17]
Media/ArmBuild/1.jpg

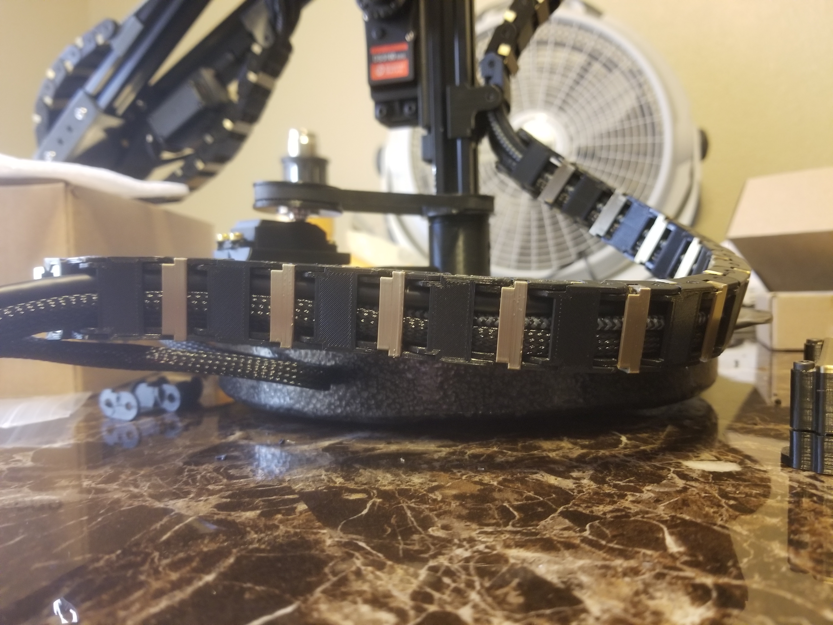
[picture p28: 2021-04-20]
Media/ArmBuild/7.jpg

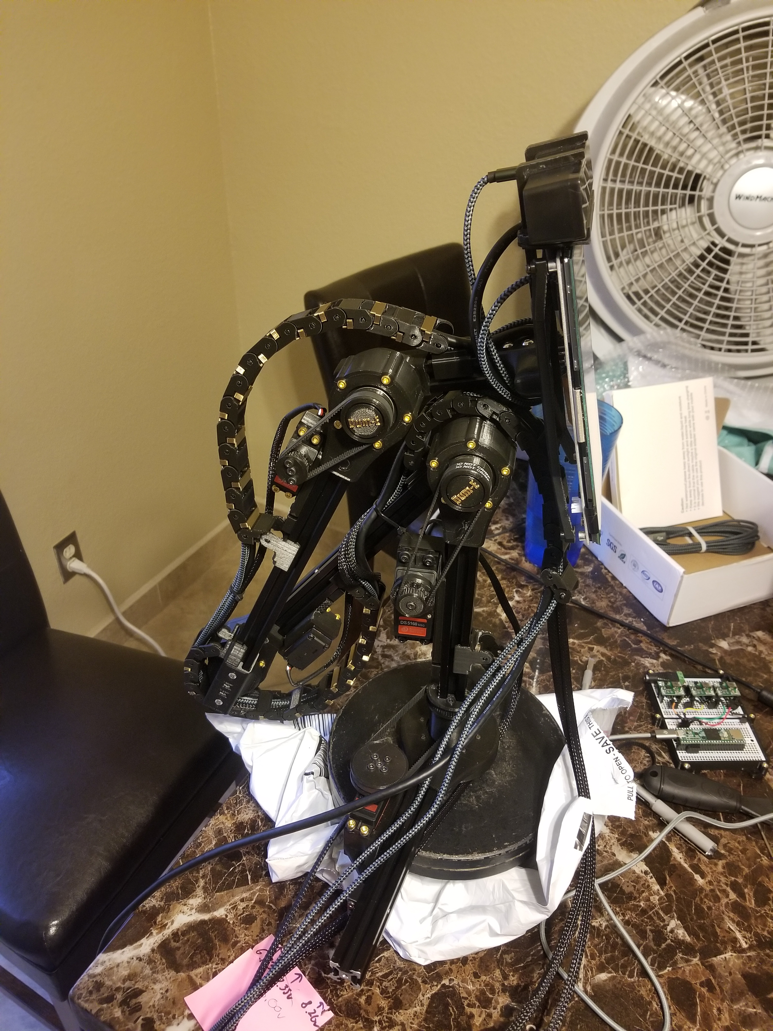
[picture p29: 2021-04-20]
Media/ArmBuild/6.jpg

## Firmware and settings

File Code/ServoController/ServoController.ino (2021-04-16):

#include <Servo.h>
#include "StringSplitter.h"
#include <EEPROM.h>

// Arm rotors 
Servo a1Servo;
Servo a2Servo;
Servo a3Servo;
Servo a4Servo;

const int servoPins[] = {20,21,22,23};

// Arm angles
float a1 = 142.0;
float a2 = 180.0-76.0;
float a3 = 142.0;
float a4 = 90.0/1.5;

// Arm angles
float a1Last = a1;
float a2Last = a2;
float a3Last = a3;
float a4Last = a4;

float cura1 = a1;
float cura2 = a2;
float cura3 = a3;
float cura4 = a4;

unsigned long servoTimer = micros();
unsigned long eepromTimer = millis();
const int eepromDelay = 2000;
const int delayTime = 100;

//Average time (in ms) between serial.write() on python script
const int timeForMessages = 10000;

//Rate of which the machine is smoothed so i runs every "milisecond" it could run faster
//to create even smoother lines but since its run on parsecs and we only have a degree of
//accuracy of about 1.2 +- some deflection it should be fine 
const float smoothingRate = float(delayTime)/float(timeForMessages);

int readMessages = 0;

unsigned long messageTimer = 0;

void setup() {
  while(!Serial){}
  a1Servo.attach(servoPins[0]);
  a2Servo.attach(servoPins[1]);
  a3Servo.attach(servoPins[2]);
  a4Servo.attach(servoPins[3]);

  //
  String angles = readStringFromEEPROM(0);
  StringSplitter *splitter = new StringSplitter(angles, ',', 4);
  String a1temp = splitter->getItemAtIndex(0);
  String a2temp = splitter->getItemAtIndex(1);
  String a3temp = splitter->getItemAtIndex(2);
  String a4temp = splitter->getItemAtIndex(3);
  
  if(a1temp >= 0 || a1temp <= 180) cura1 = a1temp.toFloat();
  if(a2temp >= 45 || a2temp <= 180) cura2 = a2temp.toFloat();
  if(a3temp >= 45 || a3temp <= 180) cura3 = a3temp.toFloat();
  if(a2temp >= 0 || a2temp <= 270) cura4 = a4temp.toFloat();

  Serial.print(String(cura1)+","+String(cura2)+","+String(cura3)+","+String(cura4));
  messageTimer = micros();
}

void loop() {
  //Reads from serial and parses into
  if (Serial.available() > 0) {
    String angles = Serial.readStringUntil('\n');
    StringSplitter *splitter = new StringSplitter(angles, ',', 4);
    String a1temp = splitter->getItemAtIndex(0);
    String a2temp = splitter->getItemAtIndex(1);
    String a3temp = splitter->getItemAtIndex(2);
    String a4temp = splitter->getItemAtIndex(3);
    // Angle checks as it seems if the python script throws an error in the buffer it will
    // throw a massive angle and the system will try to go to that massive angle
    if(a1temp >= 0 || a1temp <= 180) a1 = a1temp.toFloat();
    if(a2temp >= 45 || a2temp <= 180) a2 = abs(180.0-a2temp.toFloat());
    if(a3temp >= 45 || a3temp <= 180) a3 = a3temp.toFloat();
    if(a2temp >= 0 || a2temp <= 270) a4 = (a4temp.toFloat()/1.5);
    String eepString = String(a1) + "," + String(a2) + "," + String(a3) + "," + String(a4);
    if(millis()-eepromTimer >= eepromDelay){
      writeStringToEEPROM(0, eepString);
    }
  }
  // Controlls the speed at which the easing moves
  if((micros()-servoTimer) >= delayTime){
    angleHandler();
    servoTimer = micros();
  }
}

//Essentially if the angle is not the angle
void angleHandler(){
  if(cura1 != a1){
    cura1 = moveToAngle(a1,cura1,a1Servo);
    //Serial.print(a1);Serial.print(",");Serial.println(cura1);
  }
  if(cura2 != a2){
    cura2 = moveToAngle(a2,cura2,a2Servo);
    //Serial.print(a2);Serial.print(",");Serial.println(cura2);
  }
  if(cura3 != a3){
    cura3 = moveToAngle(a3,cura3,a3Servo);
    //Serial.print(a3);Serial.print(",");Serial.println(cura3);
  }
  if(cura4 != a4){
    cura4 = moveToAngle(a4,cura4,a4Servo);
    //Serial.print(a4);Serial.print(",");Serial.println(cura4);
  }
  //Serial.print(cura1);Serial.print(",");Serial.print(cura2);Serial.print(",");Serial.print(cura3);Serial.print(",");Serial.println(cura4);
}

//Coasts an angle from point a to point b using linear smoothing so instead of moving in one large jump it does several small jumps to attempt to give smoother movement
// You can create even more smoothing by adding a greater smoothing effect but this gives a delayed buffer that makes the algorithm overshoot
float moveToAngle(float input, float currentAngle, Servo servoName){
  float retFloat;
  float difference = abs(input-currentAngle);
  if(currentAngle > input){
    if((currentAngle - input) > (difference*smoothingRate)){
      retFloat = currentAngle-(difference*smoothingRate);
      writeToServo(servoName,retFloat);
      return retFloat;
    }
    else{
      writeToServo(servoName,input);
      return input;
    }
  }
  else if(currentAngle < input){
    if((currentAngle - input) < (-1*(difference*smoothingRate))){
      retFloat = currentAngle+(difference*smoothingRate);
      writeToServo(servoName,retFloat);
      return retFloat;
    }
    else{
      writeToServo(servoName,input);
      return input;
    }
  }
}

//Writes to the given servo a specific angle translated into parsecs to get the best degree of accuracy
void writeToServo(Servo servoName, float angle){
  int microSecondsTemp = int(2000.0*((angle)/180.0)+500.0);
  servoName.writeMicroseconds(microSecondsTemp);
  //Serial.println(microSecondsTemp);
}

String readStringFromEEPROM(int addrOffset){
  int newStrLen = EEPROM.read(addrOffset);
  char data[newStrLen + 1];
  for (int i = 0; i < newStrLen; i++){
    data[i] = EEPROM.read(addrOffset + 1 + i);
  }
  data[newStrLen] = '\0';
  return String(data);
}

void writeStringToEEPROM(int addrOffset, const String &strToWrite){
  byte len = strToWrite.length();
  EEPROM.write(addrOffset, len);
  for (int i = 0; i < len; i++){
    EEPROM.write(addrOffset + 1 + i, strToWrite[i]);
  }
}

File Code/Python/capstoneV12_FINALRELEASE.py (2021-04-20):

# AME 485/486 - Capstone
# Team: Reflection
# Members: Joshua Liska - Programming/Engineering/Fusion360 Modeling/Building
#          Ivan Mendoza - Programming/Building
#          Jack Carroll - Sound Designer/Unity Programming
#          Albert Bang - Visual Artist/Unity Programming/3D Modeling
#
# References: Emotion Model: https://drive.google.com/file/d/1192YC8mYKaCbCoACP8hTfr9PCMC2iN30/view?usp=sharing from https:/github.com/jaydeepthik/
#             Face Detection: https://realpython.com/face-detection-in-python-using-a-webcam/
#             Tkinter and general pyhton syntax
#             Two-way communication between Python 3 and Unity (C#) - Y. T. Elashry @ https://github.com/Siliconifier/Python-Unity-Socket-Communication.git
#
# Use Case: A user will step infront of the camera and the camera will then being to track that user.
# Every (delayPeriod) the emotion of the user will be taken and passed to a unity program that will also use facial reference data
# to calculate where the user is and look at them. This facial data will also be used to drive several servos to a corrected position
# and follow their movements accordingly.
#
#
# Layout of code:
# Packages
# Variables
# Computation
# Visual UI (unneccessary code aside from debugging)
# Webcam handler and webcam
# Exit Handlers
#


# Packages
import UdpComms as U
import numpy as np
from mpl_toolkits.mplot3d import Axes3D
import matplotlib.pyplot as plt
from tkinter import *
from matplotlib.figure import Figure
from matplotlib.backends.backend_tkagg import FigureCanvasTkAgg
import cv2
from PIL import Image, ImageTk
from datetime import datetime
import time
from threading import Thread
import serial
import tensorflow as tf
from tensorflow import keras
import os

os.environ['TF_CPP_MIN_LOG_LEVEL'] = '2'

#Serial Communication
#---------------------------------------------------------------------------------------------------------
try:
  ser = serial.Serial(port='COM3')
  ser.flush()
except:
  print("Serial port is not connected")

sock = U.UdpComms(udpIP="127.0.0.1", portTX=8000, portRX=8001, enableRX=True, suppressWarnings=True)

#COMPUTATION
#---------------------------------------------------------------------------------------------------------
#These variables will he changed by the serial information
# x is changed exclusively by the size of the box
# y is changed by the location of the box vertically
# z is changed by the placement of the box horizontally
x = 0
y = 40
zRotation = 135

#CONSTANTS <<LEAVE UNTOUCHED>>
#Base is technically irrelevant but it looks better to have a sized base for the graph
arm1 = 32.5
arm2 = 32.5
hand = 12.0
base = 5.0
screenSize = 17.0

#All masses assume the entirety of the mass is at the end
#of the point allowing for a larger "buffer" and less torque on the system
#Units: kg (rough rounded up estimates)
arm1Mass = .5+.09
arm2Mass = .5+.09
handMass = 1
totMass = arm1Mass + arm2Mass + handMass

#Gear ratio
gear1 = 45
gear2 = 30
gearRatio = gear1/gear2

#Units: kg/cm
a1Torque = 60*gearRatio
a2Torque = 25*gearRatio
a3Torque = 25*gearRatio

#MaxAcceptableAngles
a1MaxAngle = [0,180]
#if x is negative the angle must remain [45,90] else [45,180]
a2MaxAnglePos = [45,180]
a2MaxAngleNeg = [45,135] # Changed from [45,90] to [45,135] maybe this will allow for more backwards movement
a3MaxAngle = [0,180]
a4MaxAngle = [0,270]

facePos = [0,0,0,0]
facialEmotion = ""

#Variable for if a face isnt detected for a period of time then
noFaceDetected = 10
noFaceTime = 10

# Takes off 40% to ensure the system is not overloading
# Servos are also sold as holding torque not rotational torque
def acceptableRange(input):
  return input*0.6

#GLOBAL INSTANCING OF MATHEMATICS VARIABLES
#-------------------------------------------------------------------
#This is used once so it doesn't need to be edited or called back to q

mLengthA1 = a1Torque/(arm1Mass+arm2Mass+handMass)
mLengthA2 = a2Torque/(arm2Mass+handMass)
mLengthA3 = a3Torque/(handMass)

maxXHigh = mLengthA1-base
maxXLow = 0.0

if ((mLengthA1+base)*(-1)) < (arm1*-1):
  maxXLow = arm1*-1
  accXLow = maxXLow
else:
  maxXLow = (mLengthA1+base)*(-1)
  accXLow = acceptableRange(maxXLow)

accXHigh = acceptableRange(maxXHigh)

maxYLowXLow = (screenSize/2.0)+base+2.0
maxYLowXHigh = (screenSize/2.0)+2.0

#End of startup variables

#MATH EQUATIONS FOR HANDLING LATER
#------------------------------------------------------------------------------
def findYHigh(x,radius):
  return np.sqrt(radius**2-x**2)

def maxYCircle(ox,oy,x,y,radius):
  return np.sqrt((x-ox)**2+(y-oy)**2)

#Calculates variables neccessary for the function during startup
def lawOfCosines(a,b,c):
  return np.arccos((a**2+b**2-c**2) / (2.0*a*b))

def distance(x1,y1,x2,y2):
  return np.sqrt((x1-x2)**2+((y1-y2)**2))

def distanceMidArm(angle):
  opp = np.cos(angle) * arm1
  adj = np.sin(angle) * arm1
  return opp, adj

def angles(x,y):
  dist = distance(x,y,0,0)
  D1 = np.arctan2(y,x)
  D2 = lawOfCosines(dist,arm1,arm2)
  A1 = D1 + D2
  A2 = lawOfCosines(arm1,arm2,dist)
  return A1, A2

def rotateX(ox,x,angle):
  return ox+np.cos(angle)*(x-ox)

def rotateZ(ox,x,angle):
  return np.sin(angle)*(x-ox)

#Establisihing global variables prior to changing them
#a1 is between base and arm1
#a2 is between arm1 and arm2
a1, a2 = angles(x,y)
mx, my = distanceMidArm(a1)
dist = distance(mx,my,x+hand,y)
#a3 is between arm2 and hand
if my <= y:
  a3 = lawOfCosines(arm2,hand,dist)
else:
  a3 = np.radians(360)-lawOfCosines(arm2,hand,dist)

#a4 is z rotation
a4 = np.radians(zRotation)

xPlot = [0,0,mx,x,x+hand]
yPlot = [0,base,my+base,y+base,y+base]

xPlot3D = [rotateX(0,x,np.radians(a4)) for x in xPlot]
zPlot3D = [rotateZ(0,x,np.radians(a4)) for x in xPlot]

# The bounds checker as its called multiple times, so to reduce code this is ran multiple times
def angleChecker(array,angle):
  if angle >= np.radians(array[0]) and angle <= np.radians(array[1]):
    return True
  else:
    return False

# Verifies the angles are properly in bounds
def angleHandler(angle1,angle2,angle3,x):
  if angleChecker(a1MaxAngle,angle1) and angleChecker(a3MaxAngle,angle3):
    if x >= 0:
      if angleChecker(a2MaxAnglePos,angle2):
        return True
      else:
        return False
    else:
      if angleChecker(a2MaxAngleNeg,angle2):
        return True
      else:
        return False
  else:
    return False

# Handles x position verification
def positionHandlerX(x):
  if x >= accXLow and x <= accXHigh:
    return True
  else:
    return False

# Handles y position verification
def positionHandlerY(x,y):
  if x >= accXLow and x <= accXHigh:
    if x >= 0:
      if y >= maxYLowXHigh and y <= findYHigh(x,arm1+arm2+base):
        return True
      else:
        return False
    else:
      if y >= maxYLowXLow and y <= findYHigh(x,arm1+arm2+base):
        return True
      else:
        return False
  else:
    return False
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

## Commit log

2021-04-16 Unity and Media Inserts
2021-04-17 3D Prints
    [20mmTSlotChainAdapter_Female.stl, 20mmTSlotChainAdapter_Female_90Degree.stl, 20mmTSlotChainAdapter_Male.stl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]
2021-04-19 Desktop set
    [25-35kgMountBeefy.stl, 60ToothMidArm.stl, BackPlate.stl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]
2021-04-20 Creating new directories
    [25-35kgMountBeefy.stl]
2021-04-20 Python and arduino final code
